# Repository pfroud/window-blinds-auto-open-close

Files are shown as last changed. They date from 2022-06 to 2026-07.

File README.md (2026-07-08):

# Window blinds automatic open/close gadget

I want to block harsh reflected sunlight in the early mornings, but I also want daylight to enter my room later in day.

This device automatically closes window blinds before sunrise, then opens the window blinds at a time specified by the user.

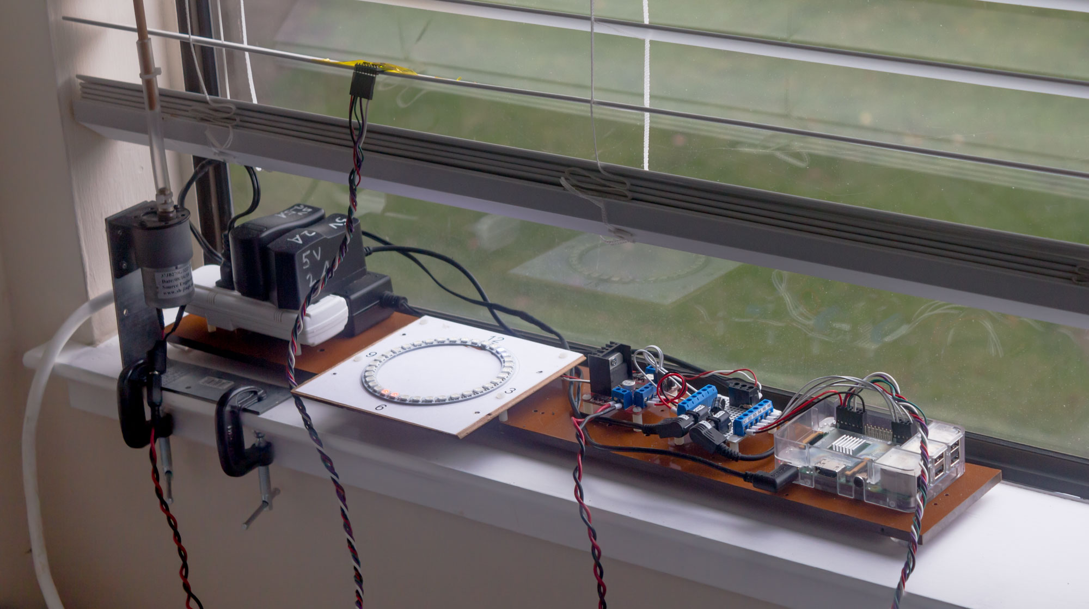
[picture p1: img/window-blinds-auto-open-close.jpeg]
Photo of device to automatically open & close window blinds


## Window blinds terminology

* The opaque white rectangles which block light when they are parallel to the window are called **slats**. 

* To rotate the slats by hand, you rotate a stick called a **wand**.

## Hardware

A motor rotates the wand to open & close the blinds. An accelerometer taped to one of the slats provides feedback. A Raspberry Pi keeps track of time, controls the motor, and monitors the accelerometer. The time is displayed on a ring of addressable RGB LEDs.

<!-- https://mermaid-js.github.io/mermaid/#/flowchart -->
```mermaid
graph LR;
    rpi[Raspberry Pi<br>v3 Model B] --- MotorDriver[Motor driver<br>L298N module] --- motor[DC gearmotor] --- WindowBlindsWand[Window blinds wand];
    rpi --- Accelerometer[Accelerometer<br>MPU-6050]
    rpi --- clock[Addressable RGB LED clock];
```

The accelerometer module also contains a gyroscope, which is not used in this project.

There are three power supplies: 5V for the Raspberry Pi, another 5V with more current for the addressable RGB LEDs, and 24V for the motor.

A little prototype board with a bunch of screw terminals helps manage wiring. It also houses a capacitor and resistor as recommended in the [Adafruit NeoPixel Überguide](https://learn.adafruit.com/adafruit-neopixel-uberguide/basic-connections).

For this project I purchased a [DuPont](https://www.mattmillman.com/info/crimpconnectors/dupont-and-dupont-connectors/) crimp tool AND a ferrule crimp tool. Both are a joy to use and made the wiring much nicer.

### Motor

The motor is made by Source Engineering Inc and has this ridiculously long model number:

   > 37JB270G/32ZYT30-2468

I got it at HSC Electronics (rest in peace) in 2018. Here's a picture of the label, which lists some slightly interesting specs:

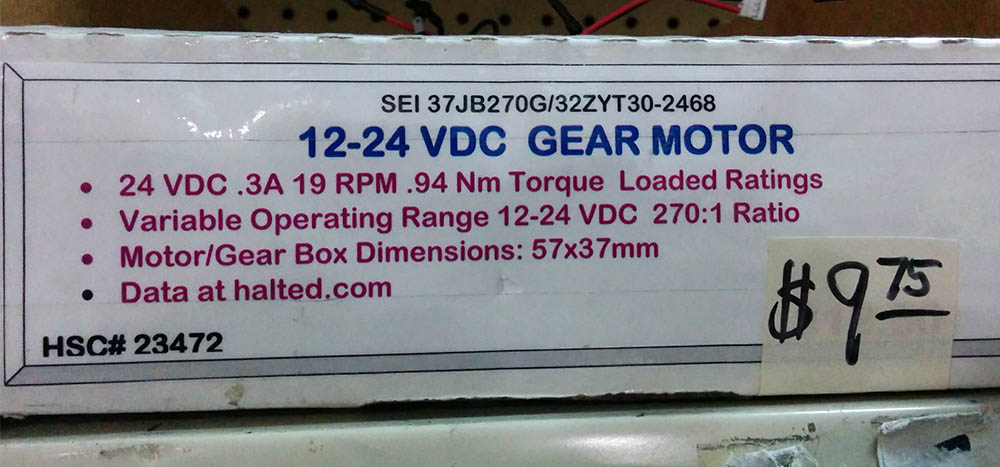
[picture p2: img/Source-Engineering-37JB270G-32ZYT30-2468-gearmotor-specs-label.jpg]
Printed label on cardboard box listing specifications for Source Engineering Inc 37JB270G/32ZYT30-2468 gearmotor


### Motor mounting plate

The motor has a bolt hole circle which is **31 (thirty-one) millimeters** in diameter.

Surely that's a mistake and it's actually 30 (thirty) mm... no, it really is 31 (thirty-one) mm.

Amazingly, 31mm is normal for this size of gearmotor. The key is that the outside diameter of the gearbox is **37 (thirty-seven) millimeters**. 

Searching for "31mm gearmotor mount" returns a scattering of suitable mounting plates. Searching for "37mm gearmotor mount" instead returns tons of results for what we want.

I had such a hard time figuring this out that I am stealing pictures from the internet, editing them, and re-hosting them in this Git repository:

<table>
<tr>
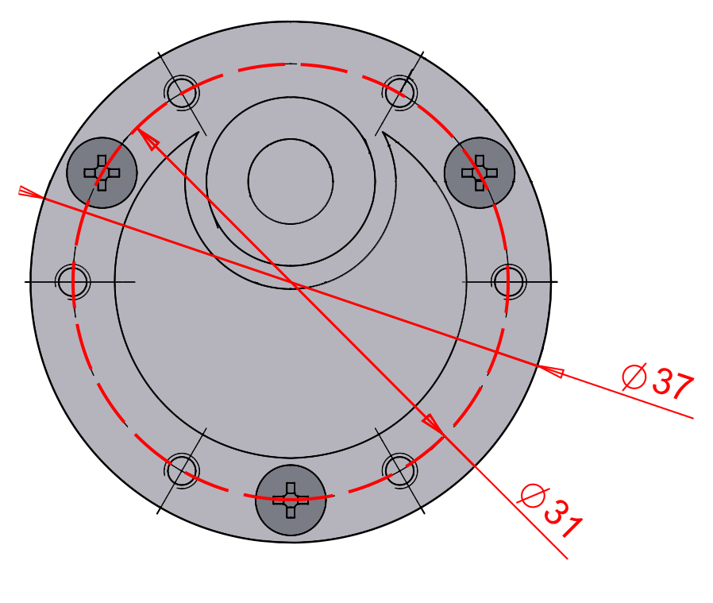
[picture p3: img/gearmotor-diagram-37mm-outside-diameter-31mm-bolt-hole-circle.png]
Diagram of gearmotor with 37mm outside diameter and 31mm bolt hole circle
<td width="67%"></td>
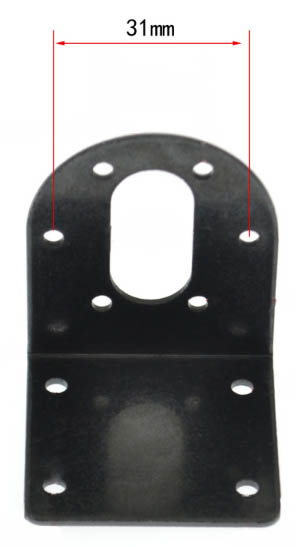
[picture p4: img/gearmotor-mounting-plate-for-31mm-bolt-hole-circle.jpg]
Mounting plate for gearmotor with 31mm bolt hole circle
<td></td>
</tr>
</table>

The holes have M3 threads. There are usually five or six of them.

### Other mounting stuff

* A [Simpson Strong-Tie A44](https://www.homedepot.com/p/Simpson-Strong-Tie-4-9-16-in-x-4-3-8-in-x-1-1-2-in-Galvanized-Angle-A44/100375040) angle bracket is the perfect size to support the motor mounting plate.

* Two adorable [one-inch C-clamps](https://www.harborfreight.com/1-inch-c-clamp-37842.html) hold the angle bracket onto the windowsill.

* Some M3 machine screws & nuts hold all the metal parts together.

* A 1/4-inch diameter wooden dowel replaces the original window blinds wand.

* A piece of 1/4-inch inside diameter vinyl tube zip-tied to the motor shaft and dowel acts as a torque-limiting flexible shaft coupler.

### Addressable RGB LED clock

I want to see what time the Raspberry Pi thinks it it, and when it will open/close the blinds, without leaving a computer monitor on.

I'm using a generic WS2812B addressable LED (Neopixel) ring, 35 LEDs, 96mm outside diameter. 

A logic level shifter is theoretically needed because the Raspberry Pi GPIO is 3.3V but the addressable LEDs operate on 5V. For some reason, my setup has always worked fine without a logic level shifter.

Here is a prototype I used to work out the logic: https://editor.p5js.org/pfroud/sketches/SYHjqIggA

## Software

Screenshot of low-quality GUI:

<p align="center">
    <!-- use HTML to center the image -->
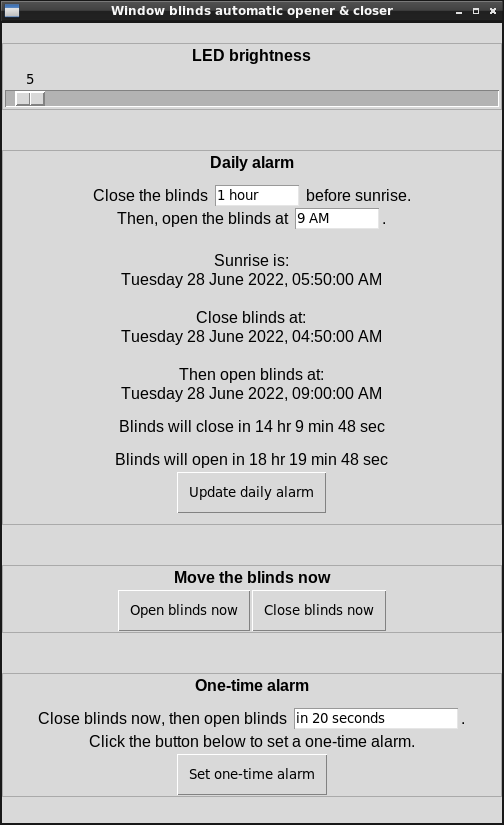
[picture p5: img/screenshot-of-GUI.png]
screenshot of GUI
    
</p>

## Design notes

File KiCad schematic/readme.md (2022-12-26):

# KiCad schematic for window blinds auto open/close gadget

This KiCad project only contains schematics for documenting the wiring and connections&mdash;there is no PCB. It was made with KiCad version 6.

The root sheet (window_blinds_auto_open_close.kicad_sch) shows connections between Raspberry Pi, accelerometer, motor driver, motor, addressable LEDs, and prototype board.

A nested sheet (prototype_board.kicad_sch) shows what connection are made on the prototype board.

To learn about how to navigate hierarchical sheets, visit https://en.wikibooks.org/wiki/Kicad/eeschema/Hierarchical_Sheets#Navigating_the_hierarchy.

## Screenshots 

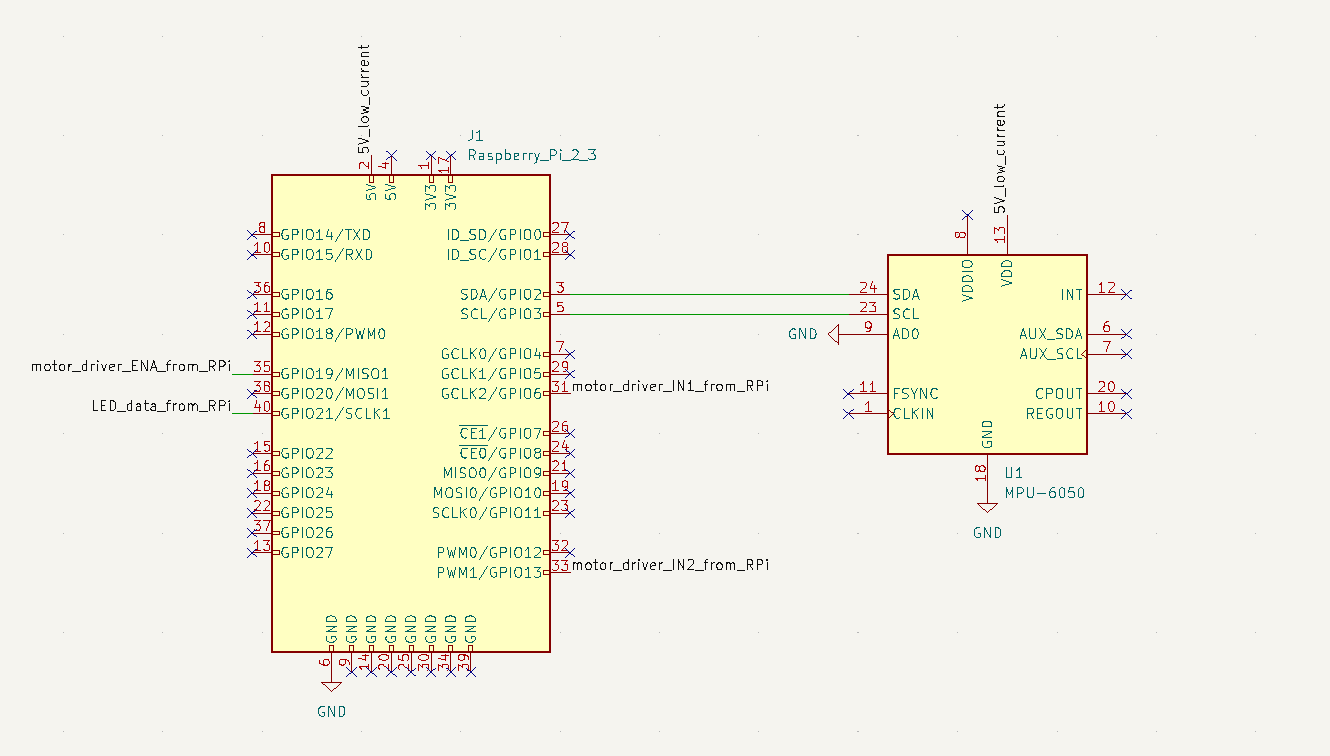
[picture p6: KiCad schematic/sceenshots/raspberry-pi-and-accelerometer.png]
screenshot fo schematic showing Raspberry Pi and accelerometer


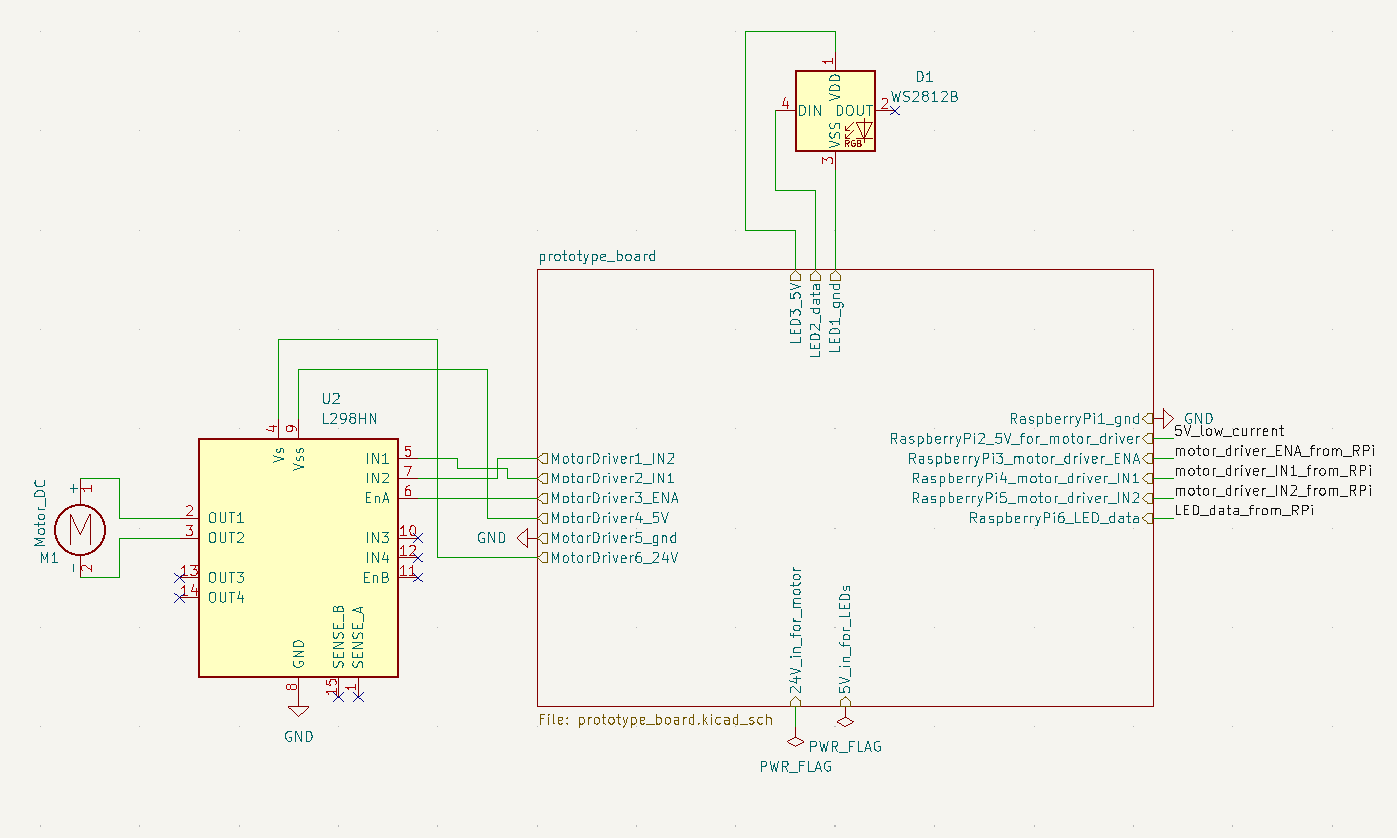
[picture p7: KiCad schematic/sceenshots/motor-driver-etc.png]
screenshot of schematic showing motor, motor driver, LED, and prototype board


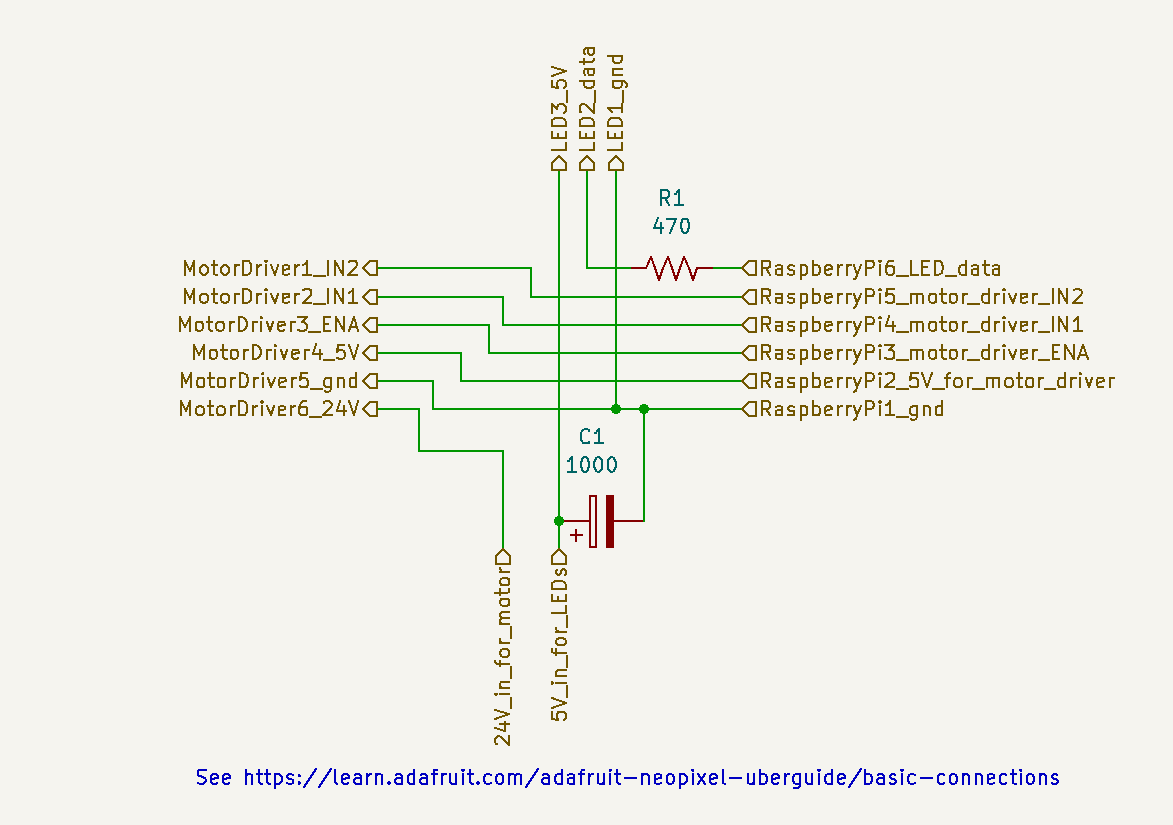
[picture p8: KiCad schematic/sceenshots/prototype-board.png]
screenshot of schematic showing a bunch of wire connections


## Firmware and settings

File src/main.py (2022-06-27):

#!/usr/bin/env python3

import os
import guizero
import requests
import traceback
import dateparser
import board
import suntime
from datetime import datetime
from datetime import timedelta
from datetime import date
from durations import Duration
from neopixel_ring_clock import NeopixelRingClock
from window_blinds import WindowBlinds

# See https://strftime.org/
DATETIME_FORMAT_STRING = "%A %d %B %Y, %I:%M:%S %p"


def timedelta_split(timedelta):
    # Apparently timedelta doesn't have a string formatting function,
    # we need to DIY it.
    # TODO support durations greater or equal to one day
    split = str(timedelta).split(":")
    hours = int(split[0])
    minutes = int(split[1])
    seconds = round(float(split[2]))
    if seconds == 60:
        seconds = 0
        minutes += 1
    if minutes == 60:
        minutes = 0
        hours += 1
    return hours, minutes, seconds


def vertical_spacer(parent, height):
    guizero.Box(parent, height=str(height))


def main():
    guizero_app = guizero.App(
        title="Window blinds automatic opener & closer",
        width=500,
        height=800)
    vertical_spacer(guizero_app, 10)

    pin_window_blinds_H_bridge_pin_1 = 13  # GPIO pin 13 == Raspberry Pi pin 33
    pin_window_blinds_H_bridge_pin_2 = 6  # GPIO pin 6 == Raspberry Pi pin 31
    pin_window_blinds_pwm = 16  # GPIO pin 16 == Raspberry Pi pin 36
    window_blinds = WindowBlinds(
        guizero_app, pin_window_blinds_H_bridge_pin_1, pin_window_blinds_H_bridge_pin_2,
        pin_window_blinds_pwm)

    pin_neopixel = board.D21  # GPIO pin 21 == Raspberry Pi pin 40
    led_count = 35
    maximum_duty_cycle = 5  # limit the led brightness
    neopixel_ring_clock = NeopixelRingClock(pin_neopixel, led_count,
                                            maximum_duty_cycle)
    neopixel_ring_clock.update()

    datetime_daily_alarm_close = None
    datetime_daily_alarm_open = None
    datetime_one_time_alarm_open = None

    vertical_spacer(guizero_app, 10)
    box_led_brightness = guizero.Box(guizero_app, width="fill")
    box_led_brightness.set_border(1, "#aaaaaa")
    guizero.Text(box_led_brightness, text="LED brightness").tk.configure(
        font=("Liberation Sans", 12, "bold"))

    def handle_led_brightness_changed():
        neopixel_ring_clock.max_brightness = int(slider_led_brightness.value)
        neopixel_ring_clock.update()
    slider_led_brightness = guizero.Slider(box_led_brightness, start=0, end=255,
                                           command=handle_led_brightness_changed, width="fill")
    slider_led_brightness.value = maximum_duty_cycle

    vertical_spacer(guizero_app, 40)
    ########################################################################
    #################### Create GUI for daily alarm ########################
    ########################################################################
    box_daily_alarm = guizero.Box(guizero_app, width="fill")
    box_daily_alarm.set_border(1, "#aaaaaa")
    guizero.Text(box_daily_alarm, text="Daily alarm").tk.configure(
        font=("Liberation Sans", 12, "bold"))
    vertical_spacer(box_daily_alarm, 10)

    # Duration before sunrise to close the blinds
    box_close_blinds_time = guizero.Box(box_daily_alarm)
    guizero.Text(box_close_blinds_time, text="Close the blinds ", align="left")
    textbox_duration_before_sunrise = guizero.TextBox(box_close_blinds_time,
                                                      align="left", text="1 hour")
    guizero.Text(box_close_blinds_time, text=" before sunrise.",
                 align="left")

    # What time to open the blinds afterwards
    box_open_blinds_time = guizero.Box(box_daily_alarm)
    guizero.Text(
        box_open_blinds_time,
        text="Then, open the blinds at ",
        align="left")
    textbox_open_blinds_time = guizero.TextBox(box_open_blinds_time,
                                               text="9 AM", align="left")
    guizero.Text(box_open_blinds_time, text=".", align="left")

    text_daily_alarm_status = guizero.Text(box_daily_alarm,
                                           text="Click the button below to set the daily alarm.")
    vertical_spacer(box_daily_alarm, 10)
    text_daily_alarm_status2 = guizero.Text(box_daily_alarm,
                                            text="Second line of status")
    vertical_spacer(box_daily_alarm, 10)
    text_daily_alarm_status3 = guizero.Text(box_daily_alarm,
                                            text="Third line of status")

    def set_daily_alarm(for_date=None):
        # Close the blinds a user-specified amount of time before sunrise.
        # Then open the blinds at a user specified absolute time.

        # Coordinates for the City of Santa Clara, California
        sun = suntime.Sun(37.354444, -121.969167)

        if for_date is None:
            # If the date to get the sunrise for isn't speficied,
            # schedule the blinds to open for the next future sunrise.
            datetime_now = datetime.now().astimezone()
            date_today = datetime_now.date()
            is_pm = datetime_now.hour > 11
            if is_pm:
                # Sunrise is always in the AM. If the current time is PM,
                # schedule the blinds to open for tomorrow's sunrise.
                date_tomorrow = date_today + timedelta(days=1)
                datetime_sunrise = sun.get_sunrise_time(
                    date_tomorrow).astimezone()

            else:
                # Check if sunrise already happened
                datetime_sunrise_today = sun.get_sunrise_time(
                    date_today).astimezone()

                if datetime_sunrise_today <= datetime_now:
                    # Sunrise already happened today. Schedule the blinds
                    # to open for tomorrow's sunrise.
                    date_tomorrow = date_today + timedelta(days=1)
                    datetime_sunrise = sun.get_sunrise_time(
                        date_tomorrow).astimezone()
                else:
                    # Sunrise is in the future today.
                    datetime_sunrise = datetime_sunrise_today

        else:
            # Use the date given in the keywork argument.
            datetime_sunrise = sun.get_sunrise_time(for_date).astimezone()

        nonlocal datetime_daily_alarm_close

        seconds_before_sunrise = Duration(
            textbox_duration_before_sunrise.value).to_seconds()
        datetime_daily_alarm_close = (datetime_sunrise -
                                      timedelta(seconds=seconds_before_sunrise)).astimezone()

        # When to open the blinds - get an absolute time from user.
        datetime_parsed_open_at = dateparser.parse(
            textbox_open_blinds_time.value).astimezone()

        nonlocal datetime_daily_alarm_open

        if datetime_parsed_open_at is None:
            text_daily_alarm_status.text_color = "red"
            text_daily_alarm_status.value = "Couldn't parse date from string"
            datetime_daily_alarm_open = None
            return

        datetime_daily_alarm_open = datetime.combine(datetime_sunrise.date(),
                                                     datetime_parsed_open_at.time()).astimezone()

        if datetime_daily_alarm_open <= datetime_daily_alarm_close:
            text_daily_alarm_status.text_color = "red"
            text_daily_alarm_status.value = \
                "Trying to set blinds to open before they close:" + \
                "\ndatetime_daily_alarm_open = " + \
                datetime_daily_alarm_open.strftime(DATETIME_FORMAT_STRING) + \
                "\ndatetime_daily_alarm_close = " + \
                datetime_daily_alarm_close.strftime(DATETIME_FORMAT_STRING)
            datetime_daily_alarm_open = None
            return

        neopixel_ring_clock.put_alarm_region("daily",
                                             datetime_daily_alarm_close, datetime_daily_alarm_open)

        text_daily_alarm_status.text_color = "black"
        text_daily_alarm_status.value = \
            "\nSunrise is:\n" + \
            datetime_sunrise.strftime(DATETIME_FORMAT_STRING) + \
            "\n\nClose blinds at:\n" + \
            datetime_daily_alarm_close.strftime(DATETIME_FORMAT_STRING) + \
            "\n\nThen open blinds at:\n" + \
            datetime_daily_alarm_open.strftime(DATETIME_FORMAT_STRING)

    guizero.PushButton(box_daily_alarm, text="Update daily alarm",
                       command=set_daily_alarm)

    vertical_spacer(guizero_app, 40)

    #################################################################
    ############# Create GUI to move the blinds immediately #########
    #################################################################
    box_move_now = guizero.Box(guizero_app, width="fill")
    box_move_now.set_border(1, "#aaaaaa")
    guizero.Text(box_move_now, text="Move the blinds now").tk.configure(
        font=("Liberation Sans", 12, "bold"))
    vertical_spacer(box_daily_alarm, 10)

    box_move_now_content = guizero.Box(box_move_now)
    guizero.PushButton(box_move_now_content, align="left", text="Open blinds now",
                       command=window_blinds.go_to_open)
    guizero.PushButton(box_move_now_content, align="left", text="Close blinds now",
                       command=window_blinds.go_to_closed)

    vertical_spacer(guizero_app, 40)

    #################################################################
    ################## Create GUI for a one-time alarm ##############
    #################################################################
    box_one_time_alarm = guizero.Box(guizero_app, width="fill")
    box_one_time_alarm.set_border(1, "#aaaaaa")
    guizero.Text(box_one_time_alarm,
                 text="One-time alarm").tk.configure(font=("Liberation Sans", 12, "bold"))
    vertical_spacer(box_one_time_alarm, 10)

    box_one_time_alarm_time = guizero.Box(box_one_time_alarm)
    guizero.Text(box_one_time_alarm_time,
                 text="Close blinds now, then open blinds ", align="left")
    textbox_one_time_alarm = guizero.TextBox(box_one_time_alarm_time,
                                             text="in 20 seconds", align="left", width=20)
    guizero.Text(box_one_time_alarm_time, text=".", align="left")

    text_one_time_alarm_status = guizero.Text(box_one_time_alarm,
                                              text="Click the button below to set a one-time alarm.")

    def set_one_time_alarm():
        datetime_parsed = dateparser.parse(textbox_one_time_alarm.value) \
            .astimezone()
        datetime_now = datetime.now().astimezone()
        nonlocal datetime_one_time_alarm_open

        if datetime_parsed is None:
            text_one_time_alarm_status.text_color = "red"
            text_one_time_alarm_status.value = \
                "Couldn't parse date from string"
            datetime_one_time_alarm_open = None
            return

        total_seconds = (datetime_parsed - datetime_now).total_seconds()
        if total_seconds < 1:
            text_one_time_alarm_status.text_color = "red"
            text_one_time_alarm_status.value = \
                "Can't set alarm to ring in the past"
            datetime_one_time_alarm_open = None
            return

        if total_seconds >= 60 * 60 * 24:
            text_one_time_alarm_status.text_color = "red"
            text_one_time_alarm_status.value = "Setting alarm to ring " + \
                "more than one day in the future is not supported"
            datetime_one_time_alarm_open = None
            return

        datetime_one_time_alarm_open = datetime_parsed

        # Starts the blinds closing, returns immediately, does not block.
        window_blinds.go_to_closed()

        neopixel_ring_clock.put_alarm_region("one-time", datetime_now,
                                             datetime_one_time_alarm_open)
        text_one_time_alarm_status.text_color = "black"
        text_one_time_alarm_status.value = "Submitted"

    guizero.PushButton(box_one_time_alarm, text="Set one-time alarm",
                       command=set_one_time_alarm)

    def tick(debug_printouts=False):
        datetime_now = datetime.now().astimezone()

        nonlocal datetime_one_time_alarm_open
        nonlocal datetime_daily_alarm_close
        nonlocal datetime_daily_alarm_open

        if datetime_daily_alarm_close is not None:
            timedelta_to_daily_alarm_close = \
                datetime_daily_alarm_close - datetime_now
            total_seconds = timedelta_to_daily_alarm_close.total_seconds()

            if debug_printouts:
                print(
                    f"total_seconds until daily alarm close: {total_seconds}")

            if total_seconds > 0:
                hours, minutes, seconds = \
                    timedelta_split(timedelta_to_daily_alarm_close)
                text_daily_alarm_status2.value = \
                    f"Blinds will close in {hours} hr {minutes} min {seconds} sec"

            else:
                if debug_printouts:
                    print("which is leq. zero, so I am closing the blinds")

                text_daily_alarm_status2.value = \
                    f"Blinds closed at\n{datetime_now.strftime(DATETIME_FORMAT_STRING)}."
                datetime_daily_alarm_close = None
                window_blinds.go_to_closed()

        if datetime_daily_alarm_open is not None:
            timedelta_to_daily_alarm_open = \
                datetime_daily_alarm_open - datetime_now
            total_seconds = timedelta_to_daily_alarm_open.total_seconds()

            if debug_printouts:
                print(
                    f"total_seconds until daily alarm open:  {total_seconds}")

            if total_seconds > 0:
                hours, minutes, seconds = \
                    timedelta_split(timedelta_to_daily_alarm_open)
                text_daily_alarm_status3.value = \
                    f"Blinds will open in {hours} hr {minutes} min {seconds} sec"

            else:
                if debug_printouts:
                    print("    which is leq zero, so I am opening the blinds")

                text_daily_alarm_status3.value = \
                    f"Blinds opened at\n{datetime_now.strftime(DATETIME_FORMAT_STRING)}."
                datetime_daily_alarm_open = None
                window_blinds.go_to_open()
                date_tomorrow = date.today() + timedelta(days=1)
                set_daily_alarm(date_tomorrow)

        if datetime_one_time_alarm_open is not None:
            timedelta_to_one_time_alarm_open = \
                datetime_one_time_alarm_open - datetime_now
            total_seconds = timedelta_to_one_time_alarm_open.total_seconds()
            if total_seconds > 0:
                hours, minutes, seconds = \
                    timedelta_split(timedelta_to_one_time_alarm_open)
                text_one_time_alarm_status.value = f"One-time alarm will ring in {hours} hr {minutes} min {seconds} sec"
            else:
                text_one_time_alarm_status.value = f"One-time alarm rang at\n{datetime_now.strftime(DATETIME_FORMAT_STRING)}."
                datetime_one_time_alarm_open = None
                neopixel_ring_clock.remove_alarm_region("one-time")
                window_blinds.go_to_open()

        neopixel_ring_clock.update()

    set_daily_alarm()
    guizero_app.repeat(1000, tick)
    guizero_app.display()  # blocks until the guizero window is closed
    window_blinds.stop()
    neopixel_ring_clock.all_off()


if __name__ == '__main__':
    if os.geteuid() == 0:
        main()
    else:
        exit(__file__ + ": Need to run the script as root (use sudo) to access GPIO.")

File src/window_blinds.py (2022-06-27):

# -*- coding: utf-8 -*-
from mpu6050 import mpu6050
from datetime import datetime
import gpiozero
import traceback


class WindowBlinds:
    def __init__(self, guizero_app, h_bridge_pin_1, h_bridge_pin_2, pwm_pin):
        self.guizero_app = guizero_app

        # When the AD0 pin is low, the I2C address is 0x68.
        # When the AD0 pin is high, the I2C address is 0x69.
        self.accelerometer = mpu6050(0x68)

        self.use_soft_start = True

        #  9.8 m/s on the Z axis means the accelerometer is flat.
        # Zero m/s on the Z axis means the accelerometer is vertical.
        # The blinds slats do not go totally vertical, so stop closing
        # the blinds at 9.7 m/s.
        # I want the blinds to angle daylight upwards slightly, so
        # stop opening the blinds before zero m/s.
        self.accelerometer_Z_meters_per_second_blinds_closed = 5.5
        self.accelerometer_Z_meters_per_second_blinds_open = 9.7

        self.gpio_device_H_bridge_pin_1 = gpiozero.DigitalOutputDevice(
            h_bridge_pin_1)

        self.gpio_device_H_bridge_pin_2 = gpiozero.DigitalOutputDevice(
            h_bridge_pin_2)

        self.gpio_device_motor_speed = gpiozero.PWMOutputDevice(
            pwm_pin, initial_value=0, frequency=500)

    def stop(self):
        self.gpio_device_motor_speed.off()

    def go_to_open(self):
        self._go_to_accelerometer_Z_meters_per_second(
            self.accelerometer_Z_meters_per_second_blinds_open)

    def go_to_closed(self):
        self._go_to_accelerometer_Z_meters_per_second(
            self.accelerometer_Z_meters_per_second_blinds_closed)

    def _get_accelerometer_Z_meters_per_second(self):
        return self.accelerometer.get_accel_data()["z"]

    def _go_to_accelerometer_Z_meters_per_second(
            self, accelerometer_Z_meters_per_second_target):
        # call the callback function as a non-callback to start the process
        self._go_to_accelerometer_Z_meters_per_second_callback(
            datetime.now(),
            self._get_accelerometer_Z_meters_per_second(),
            accelerometer_Z_meters_per_second_target,
            None)

    def _go_to_accelerometer_Z_meters_per_second_callback(self,
                                                          datetime_initial,
                                                          accelerometer_meters_per_second_initial,
                                                          accelerometer_meters_per_second_target,
                                                          previous_is_difference_from_target_positive,
                                                          debug_printouts=False):
        try:
            accelerometer_meters_per_second_present = self._get_accelerometer_Z_meters_per_second()
        except OSError:
            # Stop the motor if can't communicate with accelerometer via I2C.
            self.stop()
            traceback.print_exc()
            return

        elapsed_seconds = (datetime.now() - datetime_initial).total_seconds()

        accelerometer_meters_per_second_difference_from_initial = accelerometer_meters_per_second_initial - \
            accelerometer_meters_per_second_present

        # Adjust these threshholds through experimentation for how much
        # backlash the window blinds have, and how noisy the acceleroemter is.
        if abs(
                accelerometer_meters_per_second_difference_from_initial) < 0.7 and elapsed_seconds > 12:
            self.stop()
            print("Stopping because the accelerometer hasn't moved enough,")
            print("probably forgot to turn on power supply for motor.")
            return

        accelerometer_meters_per_second_difference_from_target = accelerometer_meters_per_second_target - \
            accelerometer_meters_per_second_present

        is_difference_from_target_positive = accelerometer_meters_per_second_difference_from_target > 0

        crossed_zero = previous_is_difference_from_target_positive is not None \
            and previous_is_difference_from_target_positive != is_difference_from_target_positive

        is_close_enough = abs(
            accelerometer_meters_per_second_difference_from_target) < 0.05

        if debug_printouts:
            print()
            print(
                f"Accel present = {accelerometer_meters_per_second_present:5.2f} m/s")
            print(f" Elapsed time = {elapsed_seconds:5.2f} seconds")
            print(
                f"Accel initial = {accelerometer_meters_per_second_initial:5.2f} m/s    Difference from present = {accelerometer_meters_per_second_difference_from_initial:5.2f} m/s")
            print(
                f" Accel target = { accelerometer_meters_per_second_target:5.2f} m/s    Difference from present = {accelerometer_meters_per_second_difference_from_target:5.2f} m/s")
            print(f"crossed zero? " + str(crossed_zero))
            print(f"close enough? " + str(is_close_enough))

        if crossed_zero or is_close_enough:
            self.stop()
        else:
            # set direction
            if is_difference_from_target_positive:
                self.gpio_device_H_bridge_pin_1.value = 1
                self.gpio_device_H_bridge_pin_2.value = 0
            else:
                self.gpio_device_H_bridge_pin_1.value = 0
                self.gpio_device_H_bridge_pin_2.value = 1

            # set motor speed
            if self.use_soft_start:
                time_when_full_speed_starts_seconds = 3
                if elapsed_seconds < time_when_full_speed_starts_seconds:
                    self.gpio_device_motor_speed.value = elapsed_seconds / \
                        time_when_full_speed_starts_seconds
                else:
                    self.gpio_device_motor_speed.value = 1
            else:
                self.gpio_device_motor_speed.value = 1

            # schedule next call to this function
            self.guizero_app.after(
                100, self._go_to_accelerometer_Z_meters_per_second_callback,
                [
                    datetime_initial,
                    accelerometer_meters_per_second_initial,
                    accelerometer_meters_per_second_target,
                    is_difference_from_target_positive])

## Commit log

2020-10-05 having a weird double-callback problem
    [main.py, window_blinds.py]
2020-11-30 make showing regions on LED ring not suck
2020-12-13 stop motor if can't commucate with accelerometer
2020-12-13 add slider for LED brightness
2020-12-21 stop if accelerometer doesn't move soon enough
    [main.py, neopixel_ring_clock.py, window_blinds.py]
2020-12-21 add motor soft start
2020-12-21 Automatically reset the daily alarm
    [main.py]
2022-02-22 change motor driver from Cytron MD30C to ST L298
2022-06-23 Make the motor driver test script work
2022-06-23 Update neopixel GPIO pin
2022-06-26 Change motor driver test script into GUI
2022-06-26 Turn off debug printouts
2022-06-26 Accelerometer returns m/s not Gs
2022-06-27 Add buttons to open/close blinds now
2022-06-27 Add PWM frequency slider to motor test GUI
2022-06-27 Reduce PWM frequency to make soft start work better
2022-06-27 Add box for buttons to move blinds now
2022-06-27 Improve the accelerometer test script
2022-06-28 Add KiCad schematic to document the wiring
    [prototype_board.kicad_sch, window_blinds_auto_open_close.kicad_sch]
2022-12-26 Add screenshots of KiCad schematics
2022-12-26 Reduce KiCad schematic paper size
    [window_blinds_auto_open_close.kicad_sch]
